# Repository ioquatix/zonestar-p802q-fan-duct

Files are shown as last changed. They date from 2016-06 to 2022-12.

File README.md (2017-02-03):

# Zonestar P802Q Fan Duct

This repository includes a number of parts which are designed to improve the fan duct of the [Zonestar P802Q/P802QA](http://www.aliexpress.com/item/full-Metal-Reprap-Prusa-i3-3d-Printer-DIY-kit-Stainless-Steel-Easy-Installation-2-Roll-Filament/32586716087.html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) 3D printer. The design is loosely based on a [Francis Turbine](https://en.wikipedia.org/wiki/Francis_turbine).

Fan Duct Simulation

## Motivation

This printer is inexpensive and generally well built but the default fan duct leaves much to be desired. I wanted to improve bridging performance and explore turbine design.

## Parts Required

- Original M3 screws for mounting fan.
- 2x M3x12 for top fan mount.
- 2x M3x10 + bolts for fan front bracket.
- 1x M3x20 + bolt for clip to hold on duct.

## Instructions

### Fan Mount

The fan mount is usually not very accurate, so the included parts allows for some lateral alignment as required.

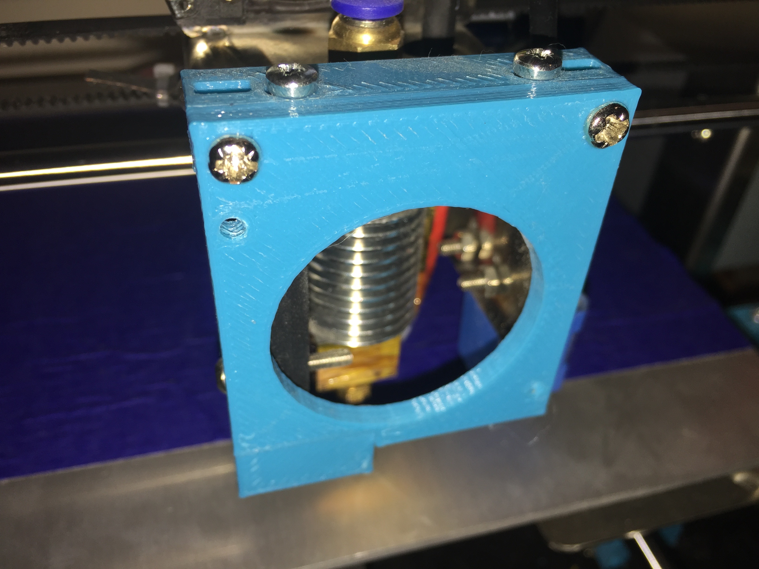
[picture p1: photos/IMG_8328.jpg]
Fan Mount


1. Print out the fan mount parts.
2. Remove the existing fan mount, and attach the new one.
3. Attach the existing fan on the mount.

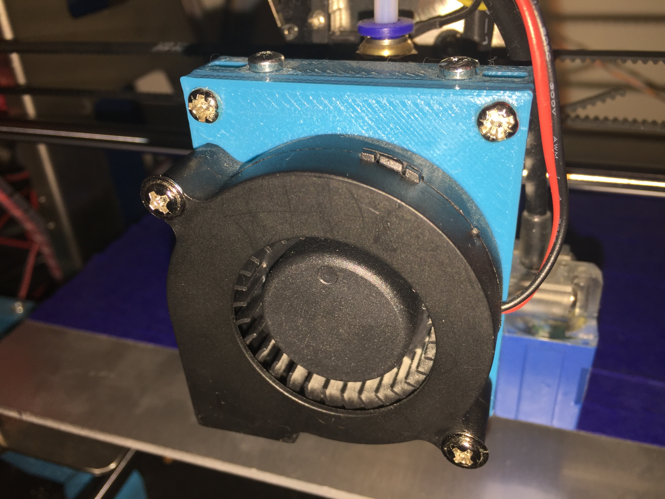
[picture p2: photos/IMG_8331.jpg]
Fan Mount with fan


### Duct Installation

The duct height is critical, and it is difficult to print. I suggest 50% perimeter overlap and minimum 1 layer perimeter, otherwise the thin walls won't print correctly to allow the top cover bridging. Additionally, I had issues using slic3r 1.2.9 so check that the bridging is being done in a way that is actually feasible before printing.

1. Print out the fan duct and clip.
2. Prepare the clip by slipping over the fan duct.
3. With some effort, slot the whole lot over the blower fan nozzle.

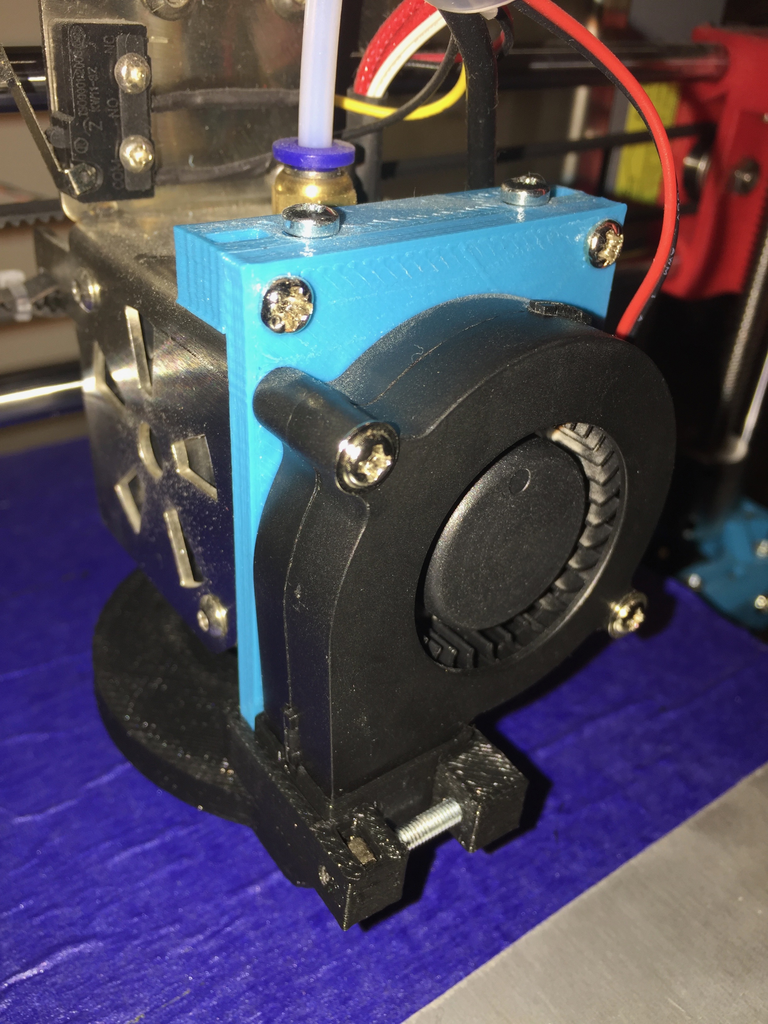
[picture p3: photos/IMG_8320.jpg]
Duct with Clip


Position the duct so that there is about 1mm clearance below (relative to the print head), and so that it is not touching the hot end either. Ensure that the duct is level with the print bed.

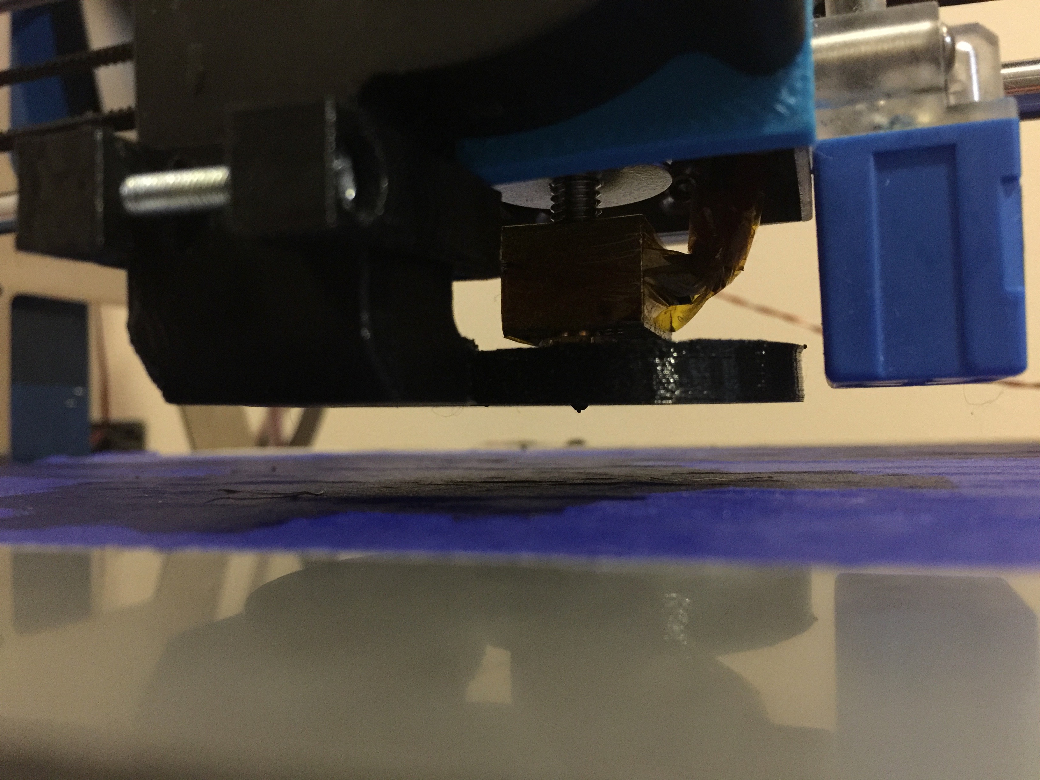
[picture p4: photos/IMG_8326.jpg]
Duct Alignment


As you can see from the following picture, some contact may occur if you are not careful. The addition of some aluminium tape may be helpful to prevent significant damage to the surface of the duct.

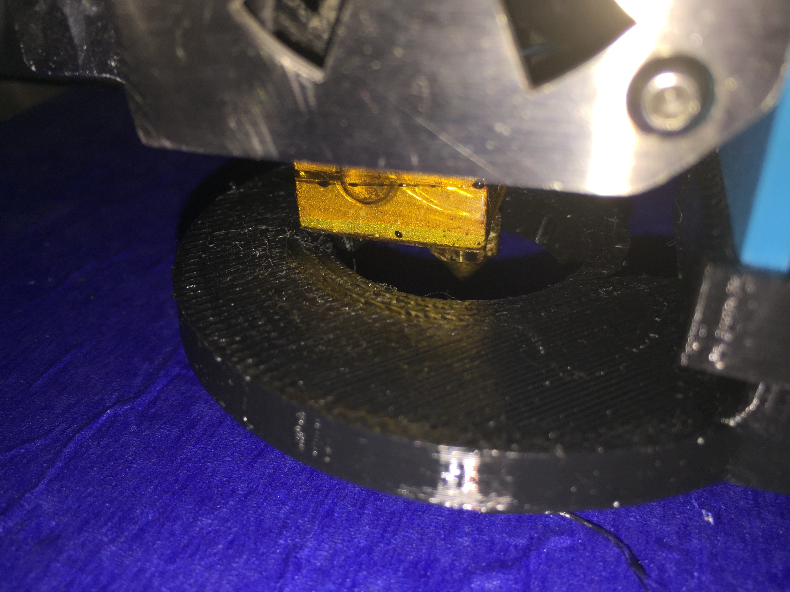
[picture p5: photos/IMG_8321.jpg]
Duct Melting


## Contributing

1. Fork it
2. Create your feature branch (`git checkout -b my-new-feature`)
3. Commit your changes (`git commit -am 'Add some feature'`)
4. Push to the branch (`git push origin my-new-feature`)
5. Create new Pull Request

## License

Released under the MIT license.

Copyright, 2016, by [Samuel G. D. Williams](http://www.codeotaku.com/samuel-williams).

Permission is hereby granted, free of charge, to any person obtaining a copy of this software and associated documentation files (the "Software"), to deal in the Software without restriction, including without limitation the rights to use, copy, modify, merge, publish, distribute, sublicense, and/or sell copies of the Software, and to permit persons to whom the Software is furnished to do so, subject to the following conditions:

The above copyright notice and this permission notice shall be included in all copies or substantial portions of the Software.

THE SOFTWARE IS PROVIDED "AS IS", WITHOUT WARRANTY OF ANY KIND, EXPRESS OR IMPLIED, INCLUDING BUT NOT LIMITED TO THE WARRANTIES OF MERCHANTABILITY, FITNESS FOR A PARTICULAR PURPOSE AND NONINFRINGEMENT. IN NO EVENT SHALL THE AUTHORS OR COPYRIGHT HOLDERS BE LIABLE FOR ANY CLAIM, DAMAGES OR OTHER LIABILITY, WHETHER IN AN ACTION OF CONTRACT, TORT OR OTHERWISE, ARISING FROM, OUT OF OR IN CONNECTION WITH THE SOFTWARE OR THE USE OR OTHER DEALINGS IN THE SOFTWARE.

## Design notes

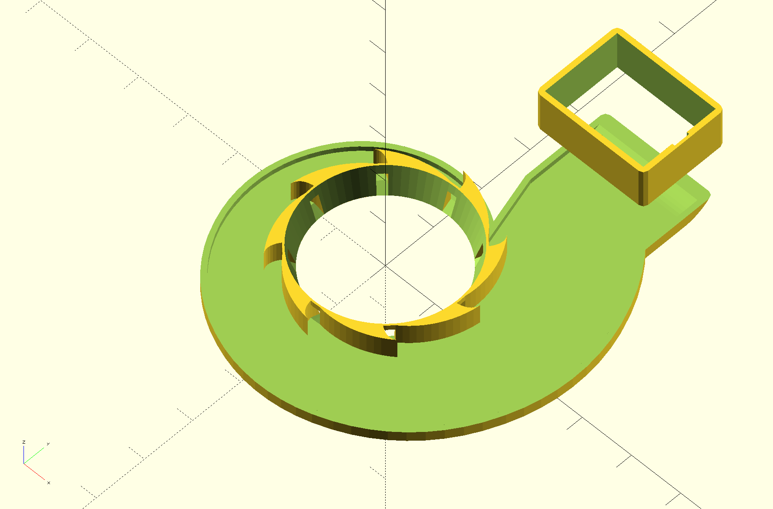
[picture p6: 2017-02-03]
photos/duct-cutout.png

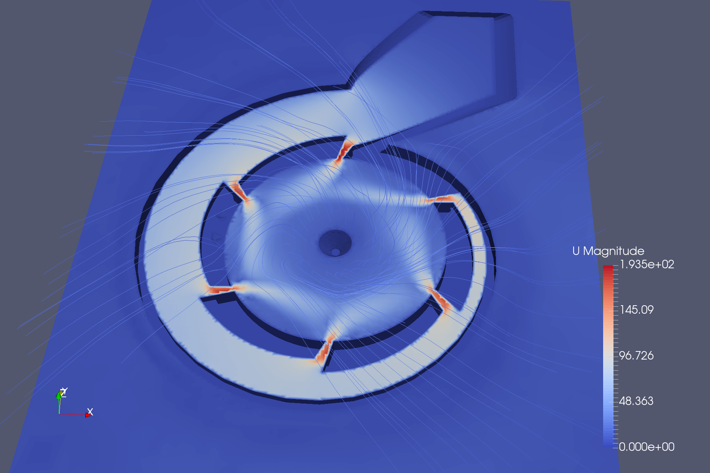
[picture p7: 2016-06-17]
photos/duct6-constant-velocity.png

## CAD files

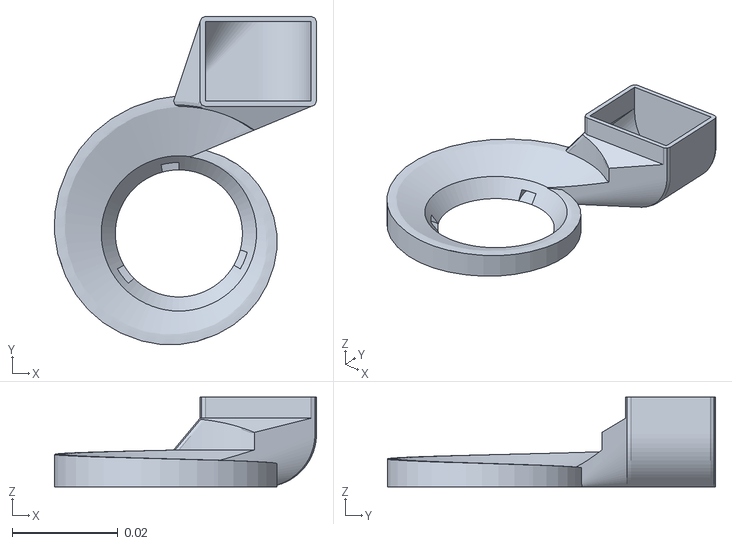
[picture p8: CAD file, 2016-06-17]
airflow/constant/triSurface/duct.stl
0.0495 x 0.062 x 0.017

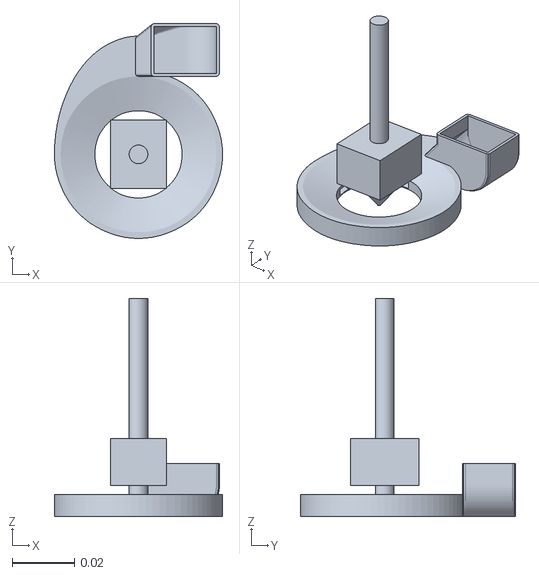
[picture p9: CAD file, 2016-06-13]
airflow/duct/constant/triSurface/turbine.stl
0.054 x 0.069 x 0.07

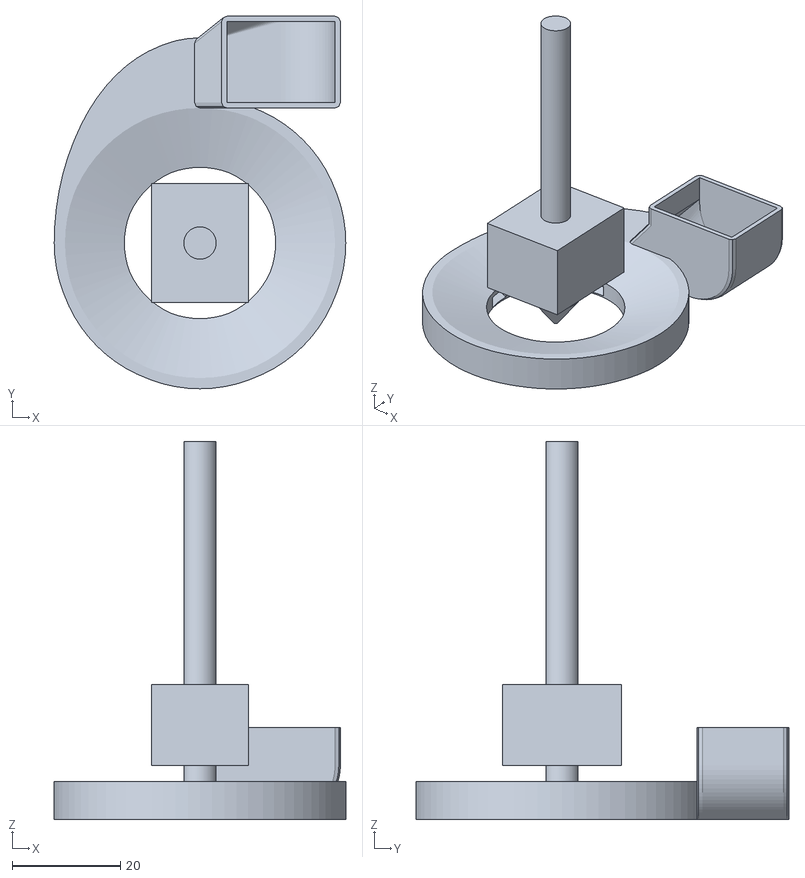
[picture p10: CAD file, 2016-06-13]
airflow/turbine_mm.stl
54.0 x 69.0 x 70.0

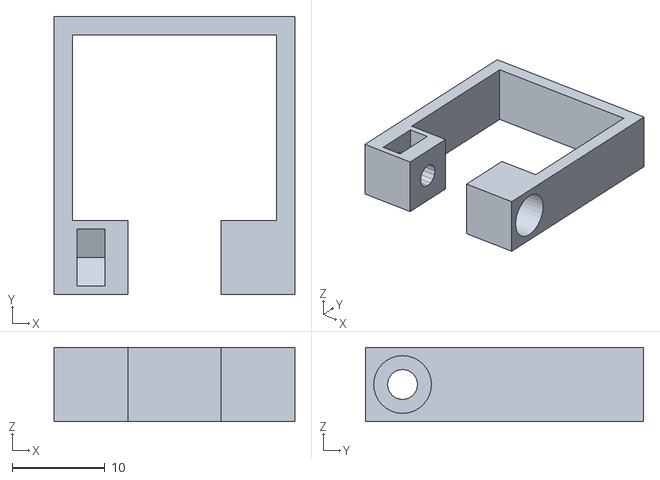
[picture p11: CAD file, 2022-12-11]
build/clip.stl
26.0 x 30.0 x 8.00

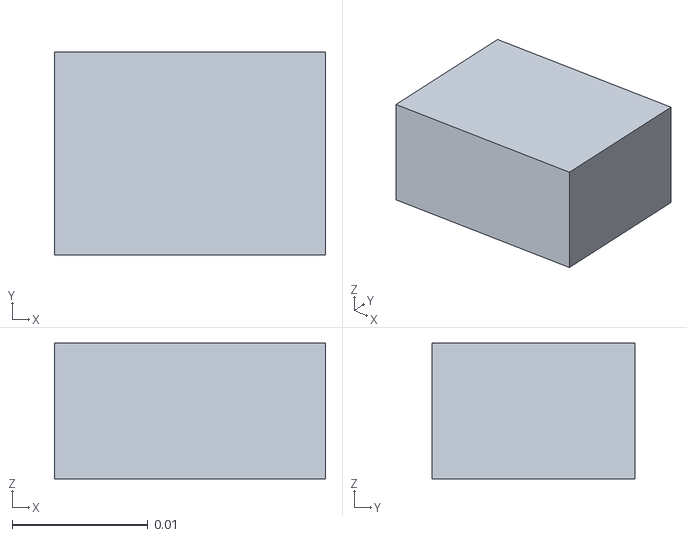
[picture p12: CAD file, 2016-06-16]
airflow/constant/triSurface/intake.stl
0.02 x 0.015 x 0.01

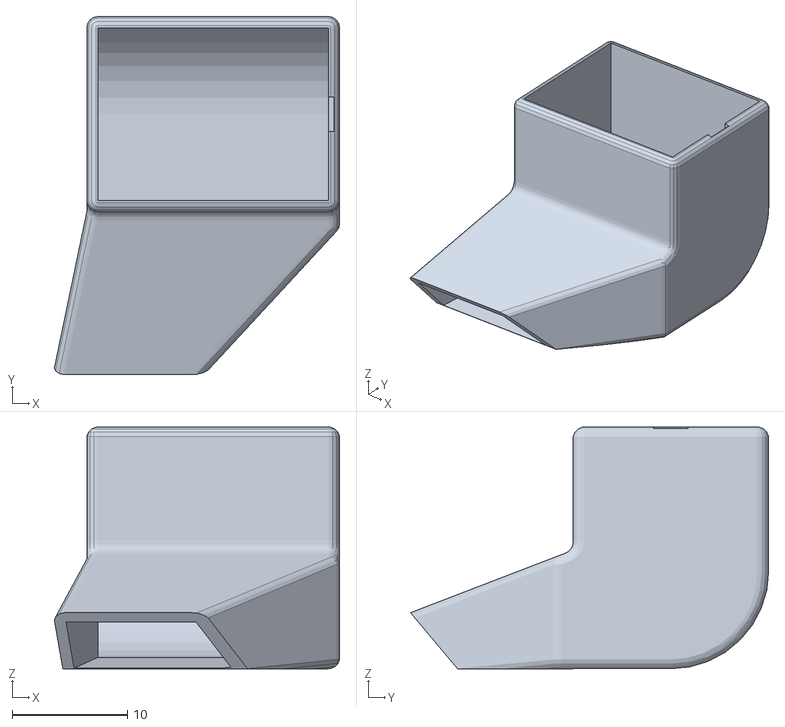
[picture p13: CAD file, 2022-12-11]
build/simple.stl
24.8 x 31.1 x 21.0

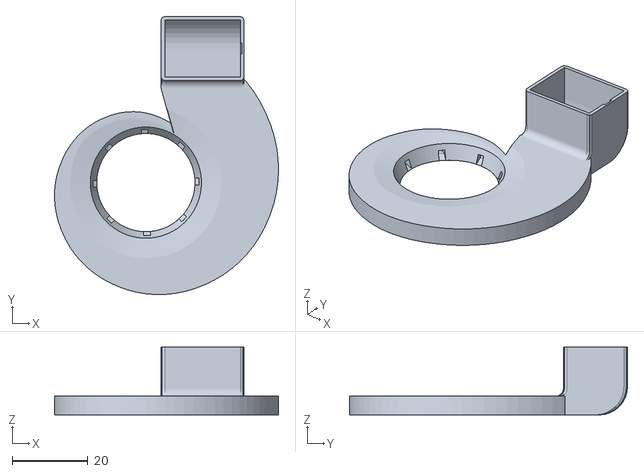
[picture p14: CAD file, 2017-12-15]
build/duct.stl
59.3 x 73.6 x 18.0

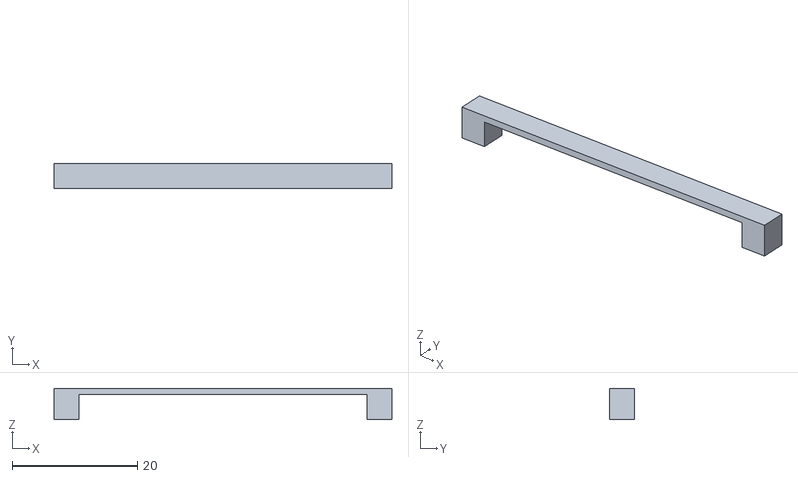
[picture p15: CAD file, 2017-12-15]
build/bridge.stl
54.0 x 4.00 x 5.00

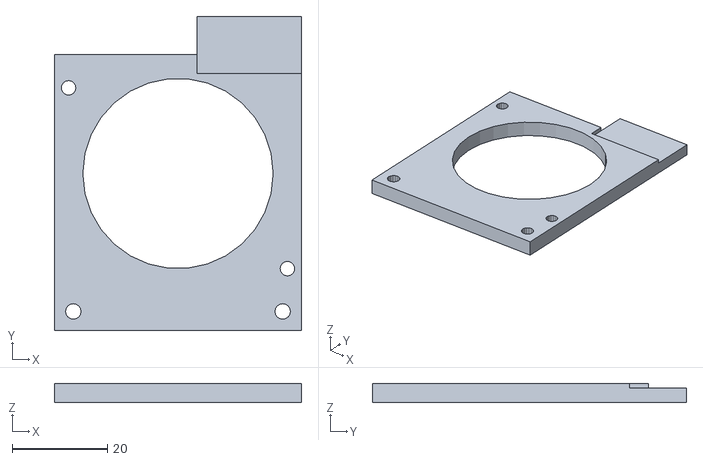
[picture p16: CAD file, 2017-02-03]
build/fan_mount_bracket.stl
52.0 x 66.0 x 4.00

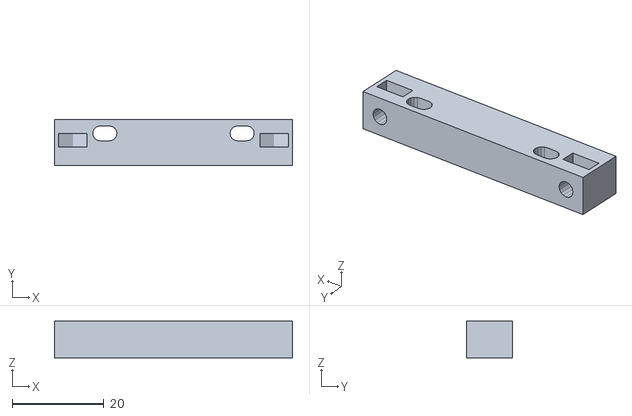
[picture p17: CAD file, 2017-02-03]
build/fan_mount_top.stl
52.0 x 10.0 x 8.00

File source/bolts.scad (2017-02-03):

$radial_error = 0.1;
$fn = 16;

module cylinder_outer(height, radius, fn=$fn, extension=0) {
	fudge = 1/cos(180/fn);
	translate([0, 0, -extension]) cylinder(h=height+extension,r=radius*fudge+$radial_error, $fn=fn);
}

module cylinder_inner(height, radius, fn=$fn, extension=0) {
	translate([0, 0, -extension]) cylinder(h=height+extension,r=radius-$radial_error,$fn=fn);
}

// Make a hole for a bolt/screw combination.
module bolt(diameter=3, depth=8, nut_offset=2, shaft_length=10, inset=10) {
	hole(diameter, depth, inset);
	hull() {
		shaft_width = diameter;
		translate([0, 0, nut_offset]) rotate(360/12, [0, 0, 1]) cylinder_outer(diameter, shaft_width, 6);
		translate([0, shaft_length, nut_offset]) rotate(360/12, [0, 0, 1]) cylinder_outer(diameter, shaft_width, 6);
	}
}

// Make a hole. The diameter is the size of the screw (e.g. 3 for M3). Depth is how far the hole should go for the thread, and inset is how far out there should be a hole for the head to go.
module hole(diameter=3, depth=6, inset=10, extension=0) {
	cylinder_outer(depth, diameter/2, extension=extension);
	translate([0, 0, depth]) cylinder_outer(inset, diameter, 32);
}

module countersunk_hole(diameter=3, depth=6, inset=10) {
	hole(diameter, depth, inset);
	translate([0, 0, depth-diameter/2]) cylinder(r1=diameter/2+$radial_error, r2=diameter+$radial_error, h=diameter/2);
}

module mounting_hole(diameter=3, depth=6, inset=10, outset=3) {
	difference() {
		cylinder_outer(depth, diameter/2+outset);
		hole(diameter=diameter, depth=depth, inset=inset);
	}
}

rotate(90, [1, 0, 0]) difference() {
	cube([30, 10, 10]);
	translate([5, 5, 0]) bolt(diameter=3, depth=8);
	translate([15, 5, 0]) bolt(diameter=4, depth=8);
	translate([25, 5, 0]) countersunk_hole(diameter=4, depth=8);
}

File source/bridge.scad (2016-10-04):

height = 4;
distance = 50;
size = 4;

translate([-distance/2, 0, 0]) cube([size, size, height]);
translate([distance/2, 0, 0]) cube([size, size, height]);
translate([-distance/2, 0, height]) cube([distance+size, size, 1]);

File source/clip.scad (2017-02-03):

use <intake.scad>;

clip();

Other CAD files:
source/duct.scad
source/fan_mount_bracket.scad
source/fan_mount_top.scad
source/intake.scad
source/interpolate.scad
source/msavazzi-duct.scad
source/simple.scad

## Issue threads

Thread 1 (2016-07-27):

License

russell, 2016-07-27:
Hey,

Sweet fan design.  I found it when i was searching for OpenFOAM simulations of 3d printer fans.  I found your video and it led me here.  I'm surprised that no one else has tried to do the same thing.  I'm going to try and re-run your simulation to see how it behaves on my full extruder assembly.

Anyway, I want to adapt your design to fit on my Prusa i3.  To be honest I'm almost done, but I can't really put it on thingiverse until you set a license.

Please consider putting a license that allows commercial use. I do 3d printing as a hobby I don't intend to make any money off your design.  But I think this design could be really valuable to the community, since you know, you actually designed and tested it, and didn't just guess how it would work.

Cheers,
Russell

ioquatix, 2017-03-14:
The MIT license DOES allow commercial use. What exactly are you referring to?

ioquatix, 2017-03-14:
Thanks for your nice comments :)

ioquatix, 2017-03-14:
Let me know how you go getting it running in OpenFOAM. I think it would be good to update it for 4.x

russell, 2017-03-14:
?  i put this comment in about almost year ago in July.  I see that you updated the readme to include a license last month.  This issue about not having an explicit license in the code base is now resolved.

ioquatix, 2017-03-14:
My bad. I didn't realise the time frame of this request. My intent was always to use the MIT license, but as this was a work in progress I took ages to get around to making an actual README which is where I always put the license. Again, apologies.

russell, 2017-03-14:
DW,  thanks for releasing this.  I'm going to take a look at it soon.  The photos you posted look impressive.

Closed 2017-03-14.

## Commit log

2016-06-09 Initial designs for airflow modelling.
    [duct.scad, intake.scad]
2016-06-09 Updated design with hotend and fan mockups.
    [bolts.scad, duct.scad, intake.scad]
2016-06-09 Improve intake ducting.
    [duct.scad, intake.scad]
2016-06-10 Initial effort to model airflow.
    [duct.scad, intake.scad, intake.stl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]
2016-06-10 Increase refinement of input STL models.
2016-06-10 Move intake up slightly.
    [intake.stl]
2016-06-10 Pressure at outlet is 0.
2016-06-10 Fix intake size.
    [intake.scad]
2016-06-11 convert to pimpleFoam, remove turbine for testing basic airflow.
    [turbine.stl]
2016-06-12 Improve duct fins.
    [duct.scad]
2016-06-12 Fix boundary conditions, update to use config from pitzDaily example.
    [intake.stl, intake_mm.stl, turbine.stl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]
2016-06-12 Correct (~) value for intake velocity.
2016-06-13 Preparing to simulate 4-vent turbine.
    [duct.scad, turbine.stl, turbine_mm.stl]
2016-06-13 Higher resolution snappyHexMeshDict copied from motorBike example.
2016-06-13 Tidy up organisation of case files.
    [duct.scad, duct.stl, intake.stl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]
2016-06-14 Updated model for new simulation.
    [duct.scad, duct.stl]
2016-06-15 Spiral seems to crash openscad.
    [duct.scad]
2016-06-15 Updated duct design using Francis Turbine style vortex generator.
    [duct.scad, duct.stl, intake.scad]
2016-06-15 Close end of vortex generator.
    [duct.scad, duct.stl]
2016-06-16 Simulating new duct design.
    [duct.scad, duct.stl, intake.stl]
2016-06-16 vortex generator now has constant velocity output from each vent.
    [duct.scad, duct.stl]
2016-06-17 Updated duct design.
    [duct.scad, duct.stl]
2016-06-17 Duct 6 outlet media.
2016-06-17 Preparing for next simulation.
    [duct.stl]
2016-06-17 Duct has improved directional output and inner wall is now sloped to reduce turbulence.
    [duct.scad, duct.stl]
2016-06-17 3 outlet duct
    [duct.stl]
2016-06-17 Test mesh is missing extruder.
    [duct.scad]
2016-06-17 Extract pressure and velocity using sample tool.
2016-06-19 First prototype printed.
    [duct.scad, duct.stl, intake.scad]
2016-10-04 Fan mount bracket, bridge, and other minor improvements.
    [bridge.scad, duct.scad, intake.scad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]
2017-02-03 Parts for final print.
    [bolts.scad, clip.scad, clip.stl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]
2017-02-03 Duct cutout.
2017-12-15 Move the duct up 3mm so that it won't bump into printed objects.
    [bridge.stl, clip.stl, duct.scad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]
2022-12-11 Add simple duct.
    [clip.stl, duct.scad, intake.scad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]
